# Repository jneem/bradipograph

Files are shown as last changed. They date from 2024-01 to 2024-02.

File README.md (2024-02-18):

# Bradipograph

A drawing robot that's kind of like a [sloth](https://en.wikipedia.org/wiki/Three-toed_sloth),
because it hangs from its arms and moves slowly.

Bradipograph writes its name (https://www.youtube.com/watch?v=CUMBa9waJp0)

This repository contains source code and CAD files for 3d printing. If you want to actually build
one, see the [bradipograph book](https://jneem.github.io/bradipograph).

## Acknowledgements

This project was based on Fredrik Stridsman's
[Stringent](https://www.hackster.io/fredrikstridsman/stringent-the-15-wall-plotter-d965ca)
wall plotter.

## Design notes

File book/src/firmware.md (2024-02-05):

# Firmware and software installation

Bradipograph needs two pieces of software to run: the firmware that gets flashed
onto the bradipograph itself, and the control software that gets run on your
computer.

## Obtain the feeder

Currently, the control software (the "feeder") is only built and tested on x86_64 linux; a statically-linked executable
is available [here](https://github.com/jneem/bradipograph/releases/latest/download/bradipo-feeder). After downloading it
and marking it executable, you should be able to run it:

```
./bradipo-feeder --help

Usage: bradipo-feeder [OPTIONS] [COMMAND]

Commands:
  calibrate        Calibrate the bradipograph from scratch
  set-arm-lengths  Re-calibrate just the arm lengths
  set-max-hang     Set the maximum vertical hang
  set-min-angle    Set the minimum hanging angle
  move             Move to a coordinate
  svg              Draw an SVG file
  square           Draw a square showing the drawable region
  query            Query the current bradipograph status
  help             Print this message or the help of the given subcommand(s)

Options:
      --simulate <SIMULATE>  If set, simulates a bradipograph and draws its output to an svg file at the given path
  -h, --help                 Print help
```

The feeder should also run on Windows and macOS, but you'll need to figure it out yourself;
the source code is [here](https://github.com/jneem/bradipograph/tree/main/crates/feeder).

## Flash the firmware

1. Install `espflash` by following its [installation instructions](https://github.com/esp-rs/espflash/blob/main/espflash/README.md#installation).
2. Download the latest bradipograph [firmware](https://github.com/jneem/bradipograph/releases/latest/download/bradipograph) and the [partition map](https://github.com/jneem/bradipograph/releases/latest/download/partition.csv).
3. Connect your ESP32-C3 (part number 5 in [Materials](./materials.md#other-parts)) to your computer with a USB cable. Your device should
   show up as a serial port; note its name. (On my linux system, it's usually `/dev/ttyACM0`.)
4. Flash your device:
    ```
    espflash flash <path/to/bradipograph> -p </path/to/serial> --partition-table <path/to/partition.csv>
     ```
    where you'll replace `<path/to/bradipograph>` with the location of the bradipograph firmware you downloaded in step 2,
    `<path/to/partition.csv>` with the location of the partition map you downloaded in step 2, and
    `</path/to/serial>` with the serial port that appeared in step 3.
5. With your ESP32-C3 still plugged in, test it by running the feeder. It should find your bradipograph device and see
   that it hasn't been calibrated yet:

   ```
   ./bradipo-feeder query
   calibration: Uncalibrated
   ```

With the firmware set up, you're ready to proceed with [assembly](./assembly.md).

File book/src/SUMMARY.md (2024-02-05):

# Summary

[Bradipograph](./introduction.md)

- [Materials](./materials.md)
- [Firmware](./firmware.md)
- [Assembly](./assembly.md)

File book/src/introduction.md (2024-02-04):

# Bradipograph: the sloth-writer

drawing of a sloth writing on a blackboard

Bradipograph is an open-source build-it-yourself robot for drawing on windows
and blackboards. Controlled over bluetooth, it can draw svgs and comes with a
library of tools for procedurally generating line drawings.

This book contains instructions to build and run your own bradipograph. Assembly
requires a 3d printer, a soldering iron, and about $20 worth of parts.

<iframe width="560" height="315" src="https://www.youtube.com/embed/CUMBa9waJp0?si=j0FrZjRh3RzgkcFA" title="Bradipograph writes its name" frameborder="0" allow="accelerometer; autoplay; clipboard-write; encrypted-media; gyroscope; picture-in-picture; web-share" allowfullscreen></iframe>

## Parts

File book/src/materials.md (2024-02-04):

# List of materials

## 3d printed parts

STL files for 3d printing are available [here](https://github.com/jneem/bradipograph/releases/tag/latest).
The required tolerances are not very tight; any reasonable print settings should be fine.

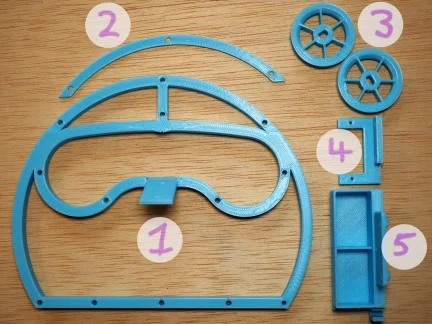
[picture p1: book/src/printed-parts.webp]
picture of 3d printed parts


1. head
2. forehead
3. rotors (you'll need two copies)
4. servo mount
5. battery box

## Other parts

Here is a picture of most of the other parts you'll need (I forgot to include the batteries). I've tried
to include Amazon and AliExpress purchase links where possible, but they tend to go stale. See the [Notes](#notes)
section for more details on the parts, and some advice on substitutions.

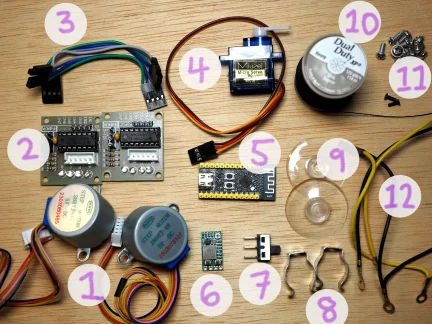
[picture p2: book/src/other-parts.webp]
picture of misc parts


1. two stepper motors (28BYJ-48) ([amazon](https://www.amazon.com/ELEGOO-28BYJ-48-ULN2003-Stepper-Arduino/dp/B01CP18J4A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), [aliexpress](https://www.aliexpress.us/item/2251832520244758.html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))
2. two stepper motor drivers (ULN2003); often sold in combination with the motors
3. the wires that came with my stepper motors and drivers. You can also just supply your own wires.
4. servo motor (sg90) ([amazon](https://www.amazon.com/Hosyond-Helicopter-Airplane-Control-Arduino/dp/B09GFN98X9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), [aliexpress](https://www.aliexpress.us/item/3256806217912283.html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))
5. ESP32-C3FH4 dev board by WeAct Studio ([aliexpress](https://www.aliexpress.us/item/3256804996835770.html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))
6. DC step down converter, 5v output ([amazon](https://www.amazon.com/gp/product/B08JZ5FVLC/ref=ppx_yo_dt_b_search_asin_title?ie=UTF8&psc=1), [aliexpress](https://www.aliexpress.us/item/3256805479283495.html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))
7. Power switch ([amazon](https://www.amazon.com/gp/product/B099N61GTZ/ref=ppx_yo_dt_b_search_asin_title?ie=UTF8&psc=1), [aliexpress](https://www.aliexpress.us/item/2255801021214741.html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))
8. Terry clips, big enough to firmly hold your markers ([amazon](https://www.amazon.com/Terry-Clips-Plastic-Coated-Spring/dp/B09MWGG883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), [aliexpress](https://www.aliexpress.us/item/3256805934884969.html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))
9. Suction cups, ([amazon](https://www.amazon.com/Pawfly-Suction-Without-Decoration-Organization/dp/B08ZS7MV1K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))
10. Thread (or fishing line)
11. A bunch of M3 screws, and two M2 screws.
12. Assorted wires, with "Dupont" style connectors and ring terminals ([amazon](https://www.amazon.com/IWISS-1550PCS-Connector-Headers-Balancer/dp/B08X6C7PZM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), [amazon](https://www.amazon.com/Terrans-Non-Insulated-Terminals-Tin-Plated-Assortment/dp/B0732XSDQX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), [aliexpress](https://www.aliexpress.us/item/3256805929468763.html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), [aliexpress](https://www.aliexpress.us/item/3256806062864141.html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,scm-url:1007.40050.354490.0,pvid:83674697-4719-4718-81c2-e83413735ee2,tpp_buckets:668%232846%238112%231997&pdp_npi=4%40dis%21USD%216.95%210.99%21%21%2149.67%217.04%21%402103010f17070748616161250eef4e%2112000036464995086%21rec%21US%21%21AB&utparam-url=scene%3ApcDetailTopMoreOtherSeller%7Cquery_from%3A))
13. Two 9v rechargeable batteries, and two 9v battery connectors (not pictured)

## Tools and equipment

- soldering iron
- 3d printer
- screwdriver
- hot glue gun
- tool for cutting and stripping wire
- crimping tool
- USB-C data cable
- computer

## Notes

### Motors and servos

28BYJ-48 stepper motors are made by many manufacturers, and often packaged
with ULN2003 drivers.
As of me writing this, a pack of 5 motors and 5 drivers is available
for $15 on Amazon or $10 on AliExpress.

The pen is lifted with an SG90 servo, which is also made by many manufacturers. A 5-pack costs about $10 on Amazon,
or $5 on AliExpress.

### The batteries

I'm using two rechargeable 9v Li-ion batteries. At about $20 for a 4-pack
on Amazon, this is definitely the most expensive part. You'll also need two 9v
battery connectors with wire leads. A 10-pack is about $5 on Amazon.

### Power supply

We'll power the device with 9v batteries, but that 9v needs to be converted
down to 5v. Adjustable DC step-down converters are available in packs
of 5 for about $10 on Amazon or $5 on AliExpress. Any cheap converter should be
fine; we won't draw much current.

### The brains

The device is controlled by an ESP32-C3 chip. Development boards with ESP32-C3
chips are available on AliExpress for as little as $2. There doesn't seem to
be much difference between the different boards except for the locations of the
various pins; probably any of them
will work. But if you want to use the exact same board as me, I'm using
WeAct Studio's ESP32-C3FH4 Core Board. This seems to be available only on AliExpress.

### Pen holder

I'm using two terry clips to hold the marker in place. You can also use a binder clip,
a rubber band, or anything else that holds the pen firmly in place.

### Wiring

I cut my own wires to approximately the correct length; I connected the wires to the
various devices using "Dupont"-style connectors, and I connected the power wires
to one another using a screw and ring terminals. You can of course use pre-cut and
pre-crimped wires if you prefer.

### String

You'll need a few meters of string for hanging the device. Ordinary sewing thread works well
(it isn't very heavy), as does fishing line.

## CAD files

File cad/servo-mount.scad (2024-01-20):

ServoDimensions = [22.5, 12.25];
WallThickness = 5;
ExtraOffset = 3;
Height = 4;
ServoScrewDistance = 27.5;
MountScrewDistance = 17;
MountScrewHeight = 8;

$fn=100;

difference() {
    translate([-ServoDimensions[0] / 2 - WallThickness, - ServoDimensions[1] / 2 - WallThickness - ExtraOffset])
    cube([ServoDimensions[0] + 2 * WallThickness, ServoDimensions[1] + WallThickness + ExtraOffset, Height]);
    cube([ServoDimensions[0] + 0.01, ServoDimensions[1] + 0.01, 20], center = true);
    
    // Screw holes for attaching to the servo
    translate([ServoScrewDistance / 2, 0, 0]) cylinder(20, r=0.95, center = true);
    translate([-ServoScrewDistance / 2, 0, 0]) cylinder(20, r=0.95, center = true);
}

translate([ServoDimensions[0] / 2 + WallThickness - MountScrewDistance / 2 - 3, 0, 0])
difference() {
    h = MountScrewHeight + 3;
    w = MountScrewDistance + 6;
    translate([0, -ServoDimensions[1]/2 - WallThickness - ExtraOffset/2, h/2])
    cube([w, ExtraOffset, h], center = true);
    
    translate([MountScrewDistance / 2, 0, MountScrewHeight])
    rotate([90, 0, 0])
    cylinder(50, r=1.5, center = true);

    translate([- MountScrewDistance/2, 0, MountScrewHeight])
    rotate([90, 0, 0])
    cylinder(50, r=1.5, center = true);
}

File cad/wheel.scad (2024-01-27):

// Diameter of (the round part of) the shaft.
ShaftDiameter = 5.0;

// Width of the flat part of the shaft;
ShaftFlatWidth = 3.0;

// The radius of the wheel, measured at the deepest part of the V
WheelRadius = 13;

// The outer radius of the hub
HubRadius = 5;

// Total thickness of the wheel
Thickness = 6;

// Radius of the rim cut-out for the string
StringRadius = 0.8;

$fs = 0.4;
$fa = 1;

module RimCrossSection() {
    t = Thickness / 2;
    rotate(-90)
    polygon([[0, 0], [t, t], [t, 0], [t/2, -t/2],
             [-t/2, -t/2], [-t, 0], [-t, t]]);
}

module Rim() {
    difference() {
        rotate_extrude()
        translate([WheelRadius, 0, 0]) 
        RimCrossSection();
        
        t = WheelRadius + StringRadius * sqrt(2);
        translate([t, 0, 0]) rotate([0, -45, 0]) cylinder(10, StringRadius, StringRadius, center = true);
        translate([t, 0, 0]) rotate([0, 45, 0]) cylinder(10, StringRadius, StringRadius, center = true);
    }
}

module Shaft() {
    intersection() {
        cylinder(Thickness * 2, ShaftDiameter / 2, ShaftDiameter / 2, center = true);
        cube([ShaftFlatWidth, ShaftDiameter * 2, Thickness * 2], center = true);
    }
}

module Hub() {
    difference() {
        cylinder(Thickness, HubRadius, HubRadius, center = true);
        Shaft();

    }
}

module Spoke2d() {
    // Distance from the end of the spoke to the origin. Should be inside the hub
    // somewhere.
    dist = ShaftDiameter / 2 + (HubRadius - ShaftDiameter / 2) / 2;
    h = WheelRadius + Thickness / 2 - dist;
    difference() {
        translate([h/2 + dist, 0])
        square([h, Thickness], center = true);
        
        translate([WheelRadius + 0.2, 0])
        minkowski() {
            translate([Thickness / 2, 0]) square([Thickness, 0.1], center = true);
            RimCrossSection();
        };
    }
}
module Spoke() {
    rotate([90, 0, 0])
    linear_extrude(1, center = true) Spoke2d();
}

module Wheel() {
for (deg = [0:60:360]) {
    rotate([0, 0, deg+30]) Spoke();
}

Hub();
Rim();
}

Wheel();

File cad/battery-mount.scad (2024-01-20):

BatterySize = [26.2, 16.9];
WallThickness = 1;
BackOffset = 2;
BoxHeight = 15;
ScrewOffset = 2.5;
ChinDepth = 2.5;
PlateWidth = 30;
PlateHeight = 15;
PowerRegulatorWidth = 11;

$fn=100;

module Box() {
    translate([-BatterySize[0] - WallThickness * 1.5, 0, 0])
    cube([BatterySize[0] * 2 + WallThickness * 3, BatterySize[1] + WallThickness * 2 + BackOffset, BoxHeight]);
    
    hull() {
        translate([-BatterySize[0] - WallThickness * 1.5, -ChinDepth, BoxHeight - 0.01])
        cube([BatterySize[0] * 2 + WallThickness * 3, ChinDepth, 0.01]);
        
        translate([-BatterySize[0] - WallThickness * 1.5, 0, BoxHeight - 0.01 - ChinDepth])
        cube([BatterySize[0] * 2 + WallThickness * 3, ChinDepth, 0.01]);
    }
}

module Battery() {
    module Right() {
        translate([WallThickness / 2, WallThickness + BackOffset, WallThickness])
        cube([BatterySize[0], BatterySize[1], 50]);
    }
    
    Right();
    mirror([1,0,0]) Right();

    // Cut the middle piece a little for better access to the screw.
    translate([-BatterySize[0] / 2, WallThickness + BackOffset, WallThickness + BoxHeight - 4])
    cube([BatterySize[0], BatterySize[1], 50]);
}

module ElectricScrewSupport() {
    h = 1.5;
    rotate([90, 0, 0])
    translate([0, 0, h/2]) cylinder(h, r1= 3, r2 = 2, center = true);
}

module Hanger() {
    module Support() {
        translate([0, BackOffset, BoxHeight + ScrewOffset - 2])
        rotate([90, 0, 0])
        linear_extrude(BackOffset)
        offset(r=2) translate([-PlateWidth / 2, 0]) square([PlateWidth, PlateHeight]);
    }

    translate([PlateWidth / 2 - 3, 0, BoxHeight + ScrewOffset + PlateHeight - 3])
    ElectricScrewSupport();
    translate([-PlateWidth / 2 + 3, 0, BoxHeight + ScrewOffset + PlateHeight - 3])
    ElectricScrewSupport();
    
    Support();
}

module ScrewHoles() {
    translate([0, 0, BoxHeight + ScrewOffset])
    rotate([90, 0, 0])
    cylinder(30, r=1.5, center = true);

    translate([PlateWidth / 2 - 3, 0, BoxHeight + ScrewOffset + PlateHeight - 3])
    rotate([90, 0, 0])
    cylinder(30, r=1.45, center = true);

    translate([-PlateWidth / 2 + 3, 0, BoxHeight + ScrewOffset + PlateHeight - 3])
    rotate([90, 0, 0])
    cylinder(30, r=1.45, center = true);
}

module PowerRegulator() {
    h = 5;
    d = 4;
    translate([0, - PowerRegulatorWidth / 2 - WallThickness, h/2])
    difference() {
        cube([d, PowerRegulatorWidth + WallThickness * 2, 5], center = true);
        translate([0, 0, WallThickness])
        cube([d + 0.01, PowerRegulatorWidth, 5.01], center = true);
    }
}

module PowerSwitch() {
    h = 10;
    d = 6;

    translate([-3.5, 0, h / 2])
    difference() {
        cube([7, d, h], center = true);
        translate([0, 0, 2]) cube([3, d + 0.01, h], center = true);
    }
}


module Positive() {
    Box();
    Hanger();

    translate([-BatterySize[0] - WallThickness * 1.5, BatterySize[1] + WallThickness * 2 + BackOffset, 0])
    PowerRegulator();

    translate([-BatterySize[0] - WallThickness * 1.5, 0, 0])
    PowerSwitch();
}

module Negative() {
    Battery();
    ScrewHoles();
}

difference() {
    Positive();
    Negative();
}

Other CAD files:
cad/main.scad

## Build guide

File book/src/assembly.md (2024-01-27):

# Assembly instructions

## Mount the motor drivers

Turn the head face-down, and place a stepper driver face-down in
the bottom left-hand corner, with the four LEDs on the driver towards
the top of the head. Secure with two M3 screws, then repeat with the other
stepper driver in the bottom right-hand corner of the head.

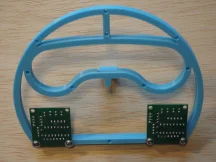
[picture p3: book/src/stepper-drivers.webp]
head with stepper drivers attached


## Attach the motors

With the head still face-down, turn one of the stepper motors axle-down
and mount it with two M3 screws to the left eye socket. The motor's wires
should point towards the bottom of the head, and slightly to the left.
Mount the other stepper motor to the right eye socket.

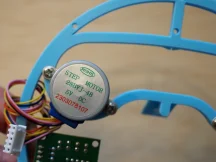
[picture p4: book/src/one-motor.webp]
head with one motor attached

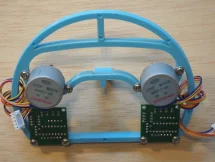
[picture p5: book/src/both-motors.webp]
head with both motors attached


## Attach the strings

Cut two long pieces of thread. Find the two holes in the rim of one
of the rotors. Starting from outside the rotor, insert the end of the
thread into one hole, then pass it between the spokes, then bring
it back out through the other hole.

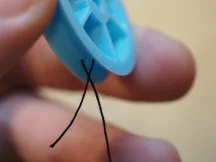
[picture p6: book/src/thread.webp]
rotor with a thread passing through the rim holes

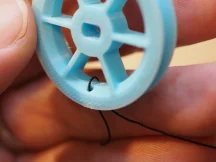
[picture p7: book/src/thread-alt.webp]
rotor with a thread passing through the rim holes, alternate angle


Tie a knot in the thread and cut off the excess.

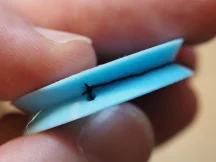
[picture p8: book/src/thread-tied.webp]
rotor with a thread tied through the rim holes


Tie the other end of the thread to one of the suction cups, and wind the thread around
the rotor.

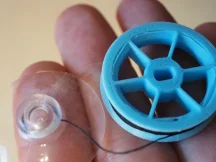
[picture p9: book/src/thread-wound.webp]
rotor with a thread wound around it


Repeat with the other rotor, thread, and suction cup.

## Mount the rotors

Turn the head face-up, and orient one rotor so that the thread winds
counter-clockwise around it. Press the rotor onto the axle of the left motor.
It should be a snug fit, and may require some force.
Pass the thread through the thread guide.

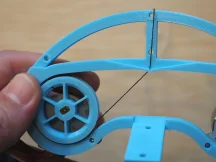
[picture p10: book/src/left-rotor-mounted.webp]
left rotor attached to the head


Mount the right rotor, oriented so that its thread winds clockwise. When
passing its thread through the thread guide, cross it over the left
rotor's thread.

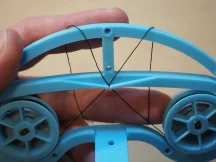
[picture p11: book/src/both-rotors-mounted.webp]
both rotors attached to the head


Wind the motor wires around the sides of the head to use up the excess,
then plug them into the motor drivers.

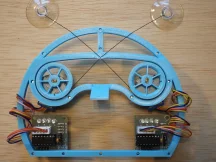
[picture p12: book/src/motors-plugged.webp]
the motor wires plugged in


Making sure that the threads are crossed, place the forehead piece over
the threads and attach it with two M3 screws. Don't attach the middle screw yet!

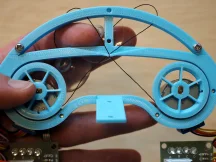
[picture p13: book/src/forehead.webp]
forehead screwed to the head


## Mount the servo

Turn the head face-down, and mount the servo bracket to the back of the head with
two M3 screws.
The servo attachment points should be on the right, and extend above the top
of the head as shown.

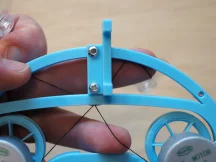
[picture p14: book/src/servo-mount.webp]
servo mounted to the head


The top screw of the servo mount must be at least 12mm, so it is long enough to
extend through the forehead.

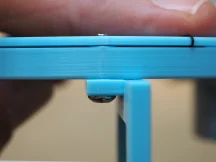
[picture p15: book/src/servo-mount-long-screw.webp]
upper servo-mount screw extending through the forehead


Insert the servo into its bracket from the right, with the servo axle towards the bottom of the head.
Fasten the servo to its bracket with two M2 screws, passing them through the servo's screw holes first
and then into the bracket.

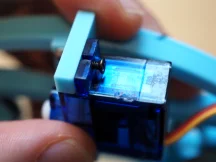
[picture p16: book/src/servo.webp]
servo mounted to the bracket

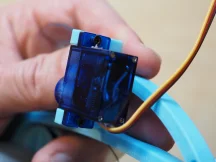
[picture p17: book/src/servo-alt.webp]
servo mounted to the bracket, alternate angle


## Attach the battery box

Attach the 9v battery connectors to the voltage converter and the power switch:
1. Solder the two positive wires from the battery connectors to center pin of the switch.
2. Join the two negative wires from the battery connector, and crimp on a ring terminal.
3. Solder a wire from one of the other switch pins to the "IN+" pin of the voltage converter.
4. Solder wires to the "GND" and "VO+" pins of the voltage converter, and crimp ring terminals
   to the other ends.

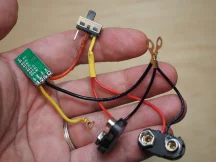
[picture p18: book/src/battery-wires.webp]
battery connectors, wired up to voltage converter and power switch


Using a hot glue gun, glue the voltage converter and the power switch to their mounting points
at the bottom left of the battery box.

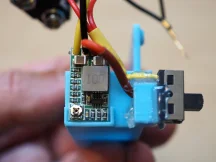
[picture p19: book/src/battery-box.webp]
voltage converter and power switch glued to the battery box

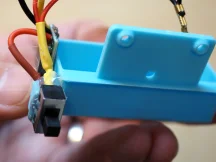
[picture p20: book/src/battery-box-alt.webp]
voltage converter and power switch glued to the battery box, alternate angle


Turn the head face-down, and use an M3 screw to attach the battery box to the bottom part of
the head, between the two stepper drivers.

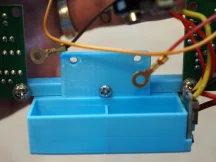
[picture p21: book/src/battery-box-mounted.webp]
battery box mounted to the head


## Attach the pen holder

Using M3 screw, attach the two spring clips to the nose.

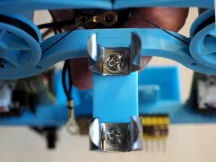
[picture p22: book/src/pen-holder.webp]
pen holder mounted to the nose


## Wire up the stepper drivers

Connect the stepper drivers to the dev board, paying close attention to the orientation.
Each stepper driver has four pins in its bottom left-hand corner; pin 1 is on the left and pin 4 is on the right.
Connect pins 1, 2, 3, and 4 of the left stepper driver to pins 0, 1, 2, and 3 respectively on the
dev board. Connect pins 1, 2, 3, and 4 of the right stepper driver to pins 4, 5, 6, and 7 respectively
on the dev board.

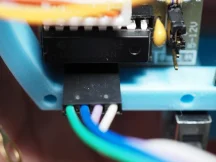
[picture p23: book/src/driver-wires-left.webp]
driver wires connected to the left driver

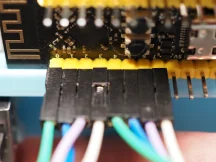
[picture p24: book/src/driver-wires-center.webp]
driver wires connected to the dev board

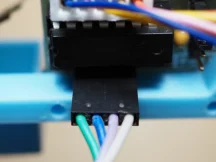
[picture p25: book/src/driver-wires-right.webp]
driver wires connected to the right driver


Cut and strip the ends of the servo motor wires. Crimp ring terminals to the ends of the red and brown
wires, and crimp a DuPont connector to the end of the yellow wire. Plug the yellow wire into pin 10 of
the dev board.

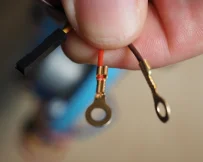
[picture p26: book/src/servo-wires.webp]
servo wire ends

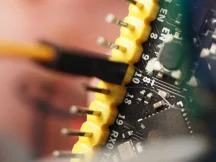
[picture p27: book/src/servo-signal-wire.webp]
servo signal wire connected to the dev board


Prepare two 2x1 DuPont connectors for providing power to the stepper drivers: first, crimp a power wire and
a ground wire to each connector. Join the two power wires and crimp them to a ring terminal, then join the
two ground wires and crimp them to another ring terminal.

## Wire up the power

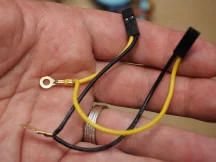
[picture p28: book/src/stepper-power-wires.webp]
stepper power wires


Plug the stepper power connectors into the stepper drivers.

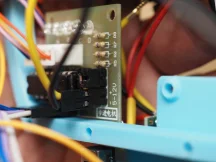
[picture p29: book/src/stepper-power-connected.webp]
stepper power wires, plugged into the drivers


Prepare a 3x1 DuPont connector for providing power to the dev board. Leaving the middle pin empty, crimp
a power wire and a ground wire into the two outer pins.

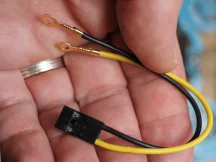
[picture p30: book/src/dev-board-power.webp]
dev board power wires


Plug in the dev board power so that the power wire connects to the pin labeled "5V" and the ground wire
connects to one of the pins labeled "G".

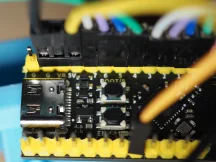
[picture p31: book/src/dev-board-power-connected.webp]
dev board power wires, plugged into the dev board


Gather all the 5V power wires (the red wire from the servo, the wire from the "VO+" pin of the voltage converter,
the stepper driver power wires, and the dev board power wire). Put an M3 screw through the ring terminals of all
these wires and screw it into the left hole on the battery box.

Gather all the ground wires (the brown wire from the servo, the wire from the "GND" pin of the voltage converter,
the stepper driver ground wires, the dev board ground wire, and the wire from the negative 9V battery terminal).
Put an M3 screw through the ring terminals of all
these wires and screw it into the right hole on the battery box.

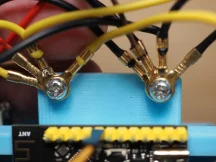
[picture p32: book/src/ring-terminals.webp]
ring terminals, all screwed together


Plug 9v batteries into the battery connectors, and put them in the battery box.

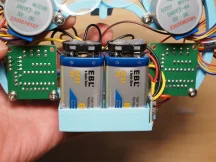
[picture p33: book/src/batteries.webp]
batteries plugged in


## Align the servo motor

Turn on the power switch. The first two leds on each stepper motor should light up, and you should here
a sound as the servo moves into position. Turn the power switch off again.

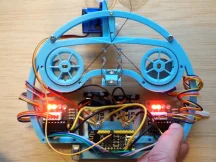
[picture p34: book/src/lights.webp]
lights on


Now that the servo has found its position, attach the little plastic piece to the servo axle so that it
points perpendicularly out from the back of the head.

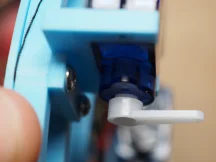
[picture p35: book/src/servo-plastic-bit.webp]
servo motor plastic bit sticking out


And that's it! Your Bradipograph is assembled and ready to draw.

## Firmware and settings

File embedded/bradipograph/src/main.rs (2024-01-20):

#![no_std]
#![no_main]
#![feature(type_alias_impl_trait)]

use core::cell::Cell;

use bradipo_geom::{Config, ConfigBuilder, LenExt as _, StepperPositions};
use bradipo_protocol::{Calibration, Cmd, StepperSegment};
use embassy_executor::Spawner;
use embassy_sync::blocking_mutex::raw::CriticalSectionRawMutex;
use embassy_time::Timer;
use embedded_storage::{ReadStorage, Storage};
use esp32c3_hal::{
    clock::{ClockControl, Clocks},
    embassy,
    ledc::{self, timer, LSGlobalClkSource, LowSpeed, LEDC},
    peripherals::Peripherals,
    prelude::*,
    systimer::{self},
    timer::TimerGroup,
    Rng, IO,
};
use esp_backtrace as _;
use esp_println::println;
use esp_storage::FlashStorage;
use esp_wifi::EspWifiInitFor;
use heapless::spsc::Queue;
use servo::Servo;
use stepper::{Direction, Stepper};

mod ble;
mod servo;
mod stepper;

macro_rules! singleton {
    ($val:expr, $T:ty) => {{
        static STATIC_CELL: ::static_cell::StaticCell<$T> = ::static_cell::StaticCell::new();
        STATIC_CELL.init($val)
    }};
}

use ble::{ble_task, CmdConsumer};

pub type Channel<T, const N: usize> = embassy_sync::channel::Channel<CriticalSectionRawMutex, T, N>;
pub type Sender<T, const N: usize> =
    embassy_sync::channel::Sender<'static, CriticalSectionRawMutex, T, N>;
pub type Receiver<T, const N: usize> =
    embassy_sync::channel::Receiver<'static, CriticalSectionRawMutex, T, N>;
pub type Mutex<T> = embassy_sync::blocking_mutex::Mutex<CriticalSectionRawMutex, T>;

const FLASH_ADDR: u32 = 0x110000;

static GLOBAL: GlobalState = GlobalState {
    config: Mutex::new(Cell::new(None)),
    position: Mutex::new(Cell::new(None)),
    pen_down: Mutex::new(Cell::new(false)),
};

struct GlobalState {
    config: Mutex<Cell<Option<Config>>>,
    position: Mutex<Cell<Option<StepperPositions>>>,
    pen_down: Mutex<Cell<bool>>,
}

impl GlobalState {
    pub fn config(&self) -> Option<Config> {
        self.config.lock(|c| c.get())
    }

    pub fn position(&self) -> Option<StepperPositions> {
        self.position.lock(|p| p.get())
    }

    pub fn pen_down(&self) -> bool {
        self.pen_down.lock(|p| p.get())
    }

    pub fn set_config(&self, config: Config) {
        self.config.lock(|c| c.set(Some(config)));
    }

    pub fn modify_config(&self, f: impl FnOnce(&mut Config)) {
        self.config.lock(|cell| {
            if let Some(mut c) = cell.get() {
                f(&mut c);
                cell.set(Some(c));
            }
        });
    }

    pub fn set_position(&self, pos: StepperPositions) {
        self.position.lock(|p| p.set(Some(pos)));
    }

    pub fn set_pen_down(&self, down: bool) {
        self.pen_down.lock(|p| p.set(down));
    }

    pub fn write_to_flash(&self) {
        if let (Some(config), Some(position)) = (self.config(), self.position()) {
            let mut buf = [0u8; 256];
            buf[0..5].copy_from_slice(b"bradi");
            let mut flash = FlashStorage::new();
            let data = FlashData { config, position };
            let _ = postcard::to_slice(&data, &mut buf[5..]).unwrap();
            flash.write(FLASH_ADDR, &buf).unwrap();
        }
    }

    pub fn read_from_flash(&self) -> Option<(Config, StepperPositions)> {
        let mut buf = [0u8; 256];
        let mut flash = FlashStorage::new();
        flash.read(FLASH_ADDR, &mut buf).unwrap();

        if &buf[0..5] == b"bradi" {
            let data = postcard::from_bytes::<FlashData>(&buf[5..]).ok()?;
            self.set_config(data.config);
            self.set_position(data.position);
            Some((data.config, data.position))
        } else {
            None
        }
    }
}

fn apply_calibration(global: &GlobalState, calib: Calibration) -> (Config, StepperPositions) {
    let radius = 1.35.cm();

    let config = if let Some(mut prev_config) = global.config() {
        prev_config.claw_distance = calib.claw_distance;
        // TODO: make these configurable, and don't override them here
        prev_config.spool_radius = radius;
        prev_config.steps_per_revolution = 2036.0;
        prev_config
    } else {
        ConfigBuilder::default()
            .with_claw_distance(calib.claw_distance)
            .with_spool_radius(radius)
            .with_max_hang(30.0.cm())
            .build()
    };

    let angles = config.arm_lengths_to_rotor_angles(&calib.arm_lengths);
    let pos = config.rotor_angles_to_stepper_steps(&angles);

    global.set_config(config);
    global.set_position(pos);
    global.write_to_flash();
    (config, pos)
}

async fn move_seg(seg: StepperSegment, left: &mut Stepper, right: &mut Stepper) {
    // This is for "underarm" orientation.
    let right_dir = if seg.right_steps > 0 {
        Direction::CounterClockwise
    } else {
        Direction::Clockwise
    };
    let left_dir = if seg.left_steps > 0 {
        Direction::Clockwise
    } else {
        Direction::CounterClockwise
    };

    for tick in seg.iter_steps() {
        Timer::after_micros(tick.delay_us.into()).await;
        if tick.left {
            left.step(left_dir);
        }
        if tick.right {
            right.step(right_dir);
        }
    }
}

async fn calibrated_control(
    mut cmds: CmdConsumer,
    left: &mut Stepper,
    right: &mut Stepper,
    servo: &mut Servo,
) {
    let mut maybe_steps = GLOBAL.position();
    loop {
        let mut written = false;
        let cmd = loop {
            if let Some(cmd) = cmds.dequeue() {
                break cmd;
            }
            if !written {
                // If we get here, our command queue is empty so let's take the
                // opportunity to write our current state to flash.
                GLOBAL.write_to_flash();
                written = true;
            }
            Timer::after_millis(2).await
        };
        match cmd {
            Cmd::Segment(seg) => {
                let Some(mut steps) = maybe_steps else {
                    println!("cannot move without a position");
                    continue;
                };

                steps.left = steps.left.checked_add_signed(seg.left_steps).unwrap();
                steps.right = steps.right.checked_add_signed(seg.right_steps).unwrap();
                maybe_steps = Some(steps);

                move_seg(seg, left, right).await;

                GLOBAL.set_position(steps);
            }
            Cmd::Calibrate(calibration) => {
                let (_, pos) = apply_calibration(&GLOBAL, calibration);

                maybe_steps = Some(pos);
            }
            Cmd::SetMinAngle(deg) => {
                GLOBAL.modify_config(|c| c.min_angle = deg);
                GLOBAL.write_to_flash();
            }
            Cmd::SetMaxHang(h) => {
                GLOBAL.modify_config(|c| c.max_hang = h);
                GLOBAL.write_to_flash();
            }
            Cmd::PenUp => {
                servo.set_angle(90).await;
                GLOBAL.set_pen_down(false);
                GLOBAL.write_to_flash();
                Timer::after_millis(500).await;
            }
            Cmd::PenDown => {
                servo.set_angle(0).await;
                GLOBAL.set_pen_down(true);
                GLOBAL.write_to_flash();
                Timer::after_millis(500).await;
            }
        }
    }
}

#[main]
async fn main(spawner: Spawner) {
    let peripherals = Peripherals::take();
    let system = peripherals.SYSTEM.split();
    let clocks = singleton!(ClockControl::max(system.clock_control).freeze(), Clocks<'_>);
    embassy::init(clocks, TimerGroup::new(peripherals.TIMG0, clocks).timer0);

    let init = esp_wifi::initialize(
        EspWifiInitFor::Ble,
        systimer::SystemTimer::new(peripherals.SYSTIMER).alarm0,
        Rng::new(peripherals.RNG),
        system.radio_clock_control,
        clocks,
    )
    .unwrap();

    let cmd_queue = singleton!(Queue::new(), Queue<Cmd, 64>);
    let (cmd_tx, cmd_rx) = cmd_queue.split();
    spawner.must_spawn(ble_task(init, peripherals.BT, cmd_tx));

    let io = IO::new(peripherals.GPIO, peripherals.IO_MUX);

    let mut right = Stepper::new(
        io.pins.gpio0.into_push_pull_output(),
        io.pins.gpio1.into_push_pull_output(),
        io.pins.gpio2.into_push_pull_output(),
        io.pins.gpio3.into_push_pull_output(),
    );
    let mut left = Stepper::new(
        io.pins.gpio4.into_push_pull_output(),
        io.pins.gpio5.into_push_pull_output(),
        io.pins.gpio6.into_push_pull_output(),
        io.pins.gpio7.into_push_pull_output(),
    );

    let ledc = singleton!(LEDC::new(peripherals.LEDC, clocks), LEDC<'static>);
    ledc.set_global_slow_clock(LSGlobalClkSource::APBClk);
    let lstimer0 = singleton!(
        ledc.get_timer::<LowSpeed>(timer::Number::Timer2),
        ledc::timer::Timer<LowSpeed>
    );
    lstimer0
        .configure(timer::config::Config {
            duty: timer::config::Duty::Duty14Bit,
            clock_source: timer::LSClockSource::APBClk,
            frequency: 50u32.Hz(),
        })
        .unwrap();
    let mut servo_channel = ledc.get_channel::<LowSpeed, _>(
        ledc::channel::Number::Channel0,
        io.pins.gpio10.into_push_pull_output(),
    );
    servo_channel
        .configure(ledc::channel::config::Config {
            timer: lstimer0,
            duty_pct: 3,
            pin_config: ledc::channel::config::PinConfig::PushPull,
        })
        .unwrap();
    let mut servo = Servo::new(servo_channel);
    servo.set_angle(90).await;

    let mut buf = [0u8; 256];
    let mut flash = FlashStorage::new();
    flash.read(FLASH_ADDR, &mut buf).unwrap();

    GLOBAL.read_from_flash();
    calibrated_control(cmd_rx, &mut left, &mut right, &mut servo).await;
}

#[derive(serde::Serialize, serde::Deserialize, Debug)]
struct FlashData {
    config: Config,
    position: StepperPositions,
}

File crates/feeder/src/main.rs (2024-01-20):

#![allow(clippy::redundant_closure_call)]

use std::{
    path::{Path, PathBuf},
    time::Duration,
};

use anyhow::anyhow;
use bradipo_geom::{Angle, ArmLengths, LenExt as _, Point};
use bradipo_protocol::{Calibration, CalibrationStatus, Cmd};
use btleplug::{
    api::{Central as _, Manager as _, ScanFilter},
    platform::Manager,
};
use clap::{builder::ValueParser, CommandFactory, FromArgMatches, Parser, Subcommand};
use connection::{BradipographLike, MockBradipograph};
use indicatif::ProgressBar;
use kurbo::{BezPath, Rect, Shape as _};
use reedline::{DefaultPrompt, DefaultPromptSegment, Prompt, Reedline};

use crate::{connection::Bradipograph, simulator::Simulation};

mod connection;
mod simulator;
mod svg;

const TICK: Duration = Duration::from_millis(50);
const MAX_STEPS_PER_SEC: u32 = 450;
// what fraction of a second does it take to reach max velocity
const MAX_VELOCITY_PER_SEC: f64 = 1.5;

#[derive(Parser)]
struct Args {
    /// If set, simulates a bradipograph and draws its output to an
    /// svg file at the given path.
    #[arg(long)]
    simulate: Option<PathBuf>,

    #[command(subcommand)]
    command: Option<Command>,
}

#[derive(Subcommand)]
enum Command {
    /// Calibrate the bradipograph from scratch
    Calibrate {
        /// distance (in cm) between the two claws
        #[arg(value_parser = ValueParser::new(sane_f32))]
        claw_distance: f32,
        /// length (in cm) of the left arm
        #[arg(value_parser = ValueParser::new(sane_f32))]
        left: f32,
        /// length (in cm) of the right arm
        #[arg(value_parser = ValueParser::new(sane_f32))]
        right: f32,
    },

    /// Re-calibrate just the arm lengths
    SetArmLengths {
        /// length (in cm) of the left arm
        #[arg(value_parser = ValueParser::new(sane_f32))]
        left: f32,
        /// length (in cm) of the right arm
        #[arg(value_parser = ValueParser::new(sane_f32))]
        right: f32,
    },

    /// Set the maximum vertical hang
    SetMaxHang {
        /// maximum distance (in cm) that we can hang below the claws
        #[arg(value_parser = ValueParser::new(sane_f32))]
        hang: f32,
    },

    /// Set the minimum hanging angle
    SetMinAngle {
        /// minimum angle (in degrees)
        #[arg(value_parser = ValueParser::new(sane_f32))]
        angle: f32,
    },

    /// Move to a coordinate
    Move {
        /// `x` coordinate (in cm), with zero being exactly between the two claws
        #[arg(value_parser = ValueParser::new(sane_signed_f32))]
        x: f32,
        /// `y` coordinate (in cm), with zero being the highest drawable position,
        /// and positive values being lower.
        #[arg(value_parser = ValueParser::new(sane_f32))]
        y: f32,
    },

    /// Draw an SVG file
    Svg {
        /// path to the svg input
        path: PathBuf,

        /// scale the output to this width (in cm)
        #[arg(value_parser = ValueParser::new(sane_f32))]
        width: Option<f32>,

        /// scale the output to this width (in cm)
        #[arg(value_parser = ValueParser::new(sane_f32))]
        height: Option<f32>,

        #[arg(long)]
        fill: bool,
    },

    /// Draw a square showing the drawable region
    Square,

    /// Query the current bradipograph status
    Query,
}

async fn reload_simulation(brad: &mut impl BradipographLike) -> Result<Simulation> {
    match brad.read_state().await? {
        CalibrationStatus::Uncalibrated => Err(anyhow!("Calibration mysteriously failed").into()),
        CalibrationStatus::Calibrated(state) => Ok(make_simulation(&state)),
    }
}

async fn calibrate(brad: &mut impl BradipographLike, calib: Calibration) -> Result<Simulation> {
    brad.send_cmd_and_wait(Cmd::Calibrate(calib)).await?;
    reload_simulation(brad).await
}

impl Command {
    async fn execute(
        &self,
        brad: &mut impl BradipographLike,
        simulation: &mut Option<Simulation>,
    ) -> Result<()> {
        match self {
            Command::Calibrate {
                claw_distance,
                left,
                right,
            } => {
                let calib = Calibration {
                    claw_distance: claw_distance.cm(),
                    arm_lengths: ArmLengths {
                        left: left.cm(),
                        right: right.cm(),
                    },
                };
                *simulation = Some(calibrate(brad, calib).await?);
            }
            Command::SetArmLengths { left, right } => match brad.read_state().await? {
                CalibrationStatus::Uncalibrated => {
                    return Err(anyhow!("set-arm-lengths requires calibration").into())
                }
                CalibrationStatus::Calibrated(state) => {
                    let calib = Calibration {
                        claw_distance: state.geom.claw_distance,
                        arm_lengths: ArmLengths {
                            left: left.cm(),
                            right: right.cm(),
                        },
                    };
                    *simulation = Some(calibrate(brad, calib).await?);
                }
            },
            Command::SetMaxHang { hang } => {
                brad.send_cmd_and_wait(Cmd::SetMaxHang(hang.cm())).await?;
                *simulation = Some(reload_simulation(brad).await?);
            }
            Command::SetMinAngle { angle } => {
                brad.send_cmd_and_wait(Cmd::SetMinAngle(Angle::degrees(*angle)))
                    .await?;
                *simulation = Some(reload_simulation(brad).await?);
            }
            Command::Move { x, y } => {
                let Some(sim) = simulation.as_mut() else {
                    return Err(anyhow!("move requires calibration").into());
                };
                let pos = Point::new(*x, *y);
                for cmd in sim.move_to(pos) {
                    brad.send_cmd(cmd).await?;
                }
            }
            Command::Svg {
                path,
                width,
                height,
                fill,
            } => {
                let Some(sim) = simulation.as_mut() else {
                    return Err(anyhow!("svg requires calibration").into());
                };
                let mut rect = sim.geom.draw_box();
                if let Some(width) = width.map(f64::from) {
                    if width < rect.width() {
                        rect.x0 = -width / 2.0;
                        rect.x1 = width / 2.0;
                    }
                }
                if let Some(height) = height.map(f64::from) {
                    if height < rect.height() {
                        let center = rect.center().y;
                        rect.y0 = center - height / 2.0;
                        rect.y1 = center + height / 2.0;
                    }
                }
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

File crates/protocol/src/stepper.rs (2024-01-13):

use serde::{Deserialize, Serialize};

/// The position of the stepper motors, measured in number of steps.
///
/// A zero value corresponds to an arm length of zero, and increasing
/// values correspond to longer arms.
#[derive(Debug, Clone, Copy, PartialEq, Eq, serde::Serialize, serde::Deserialize)]
pub struct StepperPositions {
    pub left: u32,
    pub right: u32,
}

#[derive(Clone, Debug, Serialize, Deserialize)]
pub struct StepperSegment {
    pub left_steps: i32,
    pub right_steps: i32,
    pub start_steps_per_sec: u16,
    pub end_steps_per_sec: u16,
    pub steps_per_sec_per_sec: u32,
}

impl StepperSegment {
    /// If a segment is long and the initial and final velocities are both small, the step
    /// iterator will just move along it very slowly. This is probably not what we want,
    /// though: we want to accelerate to a higher maximum speed, and then decelerate at
    /// the end.
    ///
    /// This method splits a single segment into two: an acceleration segment and a deceleration
    /// segment.
    #[cfg(feature = "std")]
    pub fn split(&self, max_steps_per_sec: u16) -> Option<(StepperSegment, StepperSegment)> {
        let start_v = self.start_steps_per_sec as f64;
        let end_v = self.end_steps_per_sec as f64;
        let max_v = max_steps_per_sec as f64;
        let max_steps_per_sec_per_sec = self.steps_per_sec_per_sec as f64;

        let square = |x| x * x;
        // How many steps would it take to get from the initial to the final velocity?
        let steps = (square(start_v) - square(end_v)).abs() / (2.0 * max_steps_per_sec_per_sec);

        let max_steps = self.left_steps.abs().max(self.right_steps.abs()) as f64;
        if max_steps == 0.0 {
            // Avoid dividing by zero.
            return None;
        }
        if steps <= max_steps / 2.0 && end_v <= max_v * 0.75 {
            // 2 * max_steps * self.accel.steps_per_s_per_s is the total amount that the squared
            // velocity can change while traversing this segment. Some of that change must be used
            // up in getting from the initial velocity to the final velocity. And then the peak energy
            // as we traverse the segment is half of what's left (since we need to go up and then down).
            let max_energy = max_steps * max_steps_per_sec_per_sec
                - (square(start_v) - square(end_v)).abs() / 2.0;
            let max_velocity = max_energy.sqrt().min(max_v);

            // How may steps will it take to get from the max velocity back down to the final velocity?
            let decel_steps =
                (square(max_velocity) - square(end_v)) / (2.0 * max_steps_per_sec_per_sec);

            let decel_seg = StepperSegment {
                left_steps: (self.left_steps as f64 * decel_steps / max_steps).round() as i32,
                right_steps: (self.right_steps as f64 * decel_steps / max_steps).round() as i32,
                start_steps_per_sec: max_velocity as u16,
                end_steps_per_sec: self.end_steps_per_sec,
                steps_per_sec_per_sec: self.steps_per_sec_per_sec,
            };
            let accel_seg = StepperSegment {
                left_steps: self.left_steps - decel_seg.left_steps,
                right_steps: self.right_steps - decel_seg.right_steps,
                start_steps_per_sec: self.start_steps_per_sec,
                end_steps_per_sec: decel_seg.start_steps_per_sec,
                steps_per_sec_per_sec: self.steps_per_sec_per_sec,
            };
            Some((accel_seg, decel_seg))
        } else {
            None
        }
    }

    pub fn iter_steps(&self) -> StepIter {
        let left = self.left_steps.unsigned_abs();
        let right = self.right_steps.unsigned_abs();

        // If either left or right doesn't move, the reciprocal is 1/0. By replacing it by MAX_PARAM,
        // we ensure that the this stepper never wins the "minimum" test that would mark it as the
        // next stepper to move.
        let recip_left_steps = MAX_PARAM.checked_div(left).unwrap_or(MAX_PARAM);
        let recip_right_steps = MAX_PARAM.checked_div(right).unwrap_or(MAX_PARAM);

        // There should be a minimum number of steps. If we say 16, it means that this can
        // be at most 2^19.
        let param_per_steps = MAX_PARAM.saturating_div(left.max(right));

        // We impose a minimum velocity so that we don't wait forever until the first step.
        // A sensible value would be sqrt(accel / 2), since that's the velocity after a
        // single step. We mostly rely on the caller to set the minimum velocity, though.
        //
        // The effect of the saturating_mul here is that the velocity will get truncated
        // if (1) it's fast and (2) there are very few steps. This truncation is probably
        // fine, because it will be over soon anyway.
        let start_param_per_t = (self.start_steps_per_sec as u32)
            .max(16)
            .saturating_mul(param_per_steps);

        let end_param_per_t = (self.end_steps_per_sec as u32)
            .max(16)
            .saturating_mul(param_per_steps);

        let param_per_t_per_t = self.steps_per_sec_per_sec.saturating_mul(param_per_steps);

        StepIter {
            left: 0,
            right: 0,
            max_left: left,
            max_right: right,
            param: 0,
            recip_left_steps,
            recip_right_steps,
            param_per_t: start_param_per_t,
            param_per_t_min: start_param_per_t.min(end_param_per_t),
            param_per_t_max: start_param_per_t.max(end_param_per_t),
            param_per_t_per_t,
            debounce: recip_right_steps.min(recip_left_steps) / 16,
            speeding_up: end_param_per_t > start_param_per_t,
        }
    }
}

#[derive(Clone, Copy, Debug)]
pub struct Tick {
    pub left: bool,
    pub right: bool,
    pub delay_us: u32,
}

const MAX_PARAM: u32 = 1 << 24;

#[derive(Debug)]
pub struct StepIter {
    // These can't actually go all the way up to u32::MAX. Up to 2^24 is probably ok, but I haven't checked carefully.
    max_left: u32,
    max_right: u32,

    // Current position.
    left: u32,
    right: u32,

    // Current parametrization, as a fraction of the distance from
    // the start position to the end position. This maxes out at 2^24.
    param: u32,

    // Current speed, in param per unit time. This goes up to 2^32 - 1, meaning
    // that the fastest we can get through the whole parameter space is about 1/256
    // of a second.
    param_per_t: u32,

    // Measured in the same units as `param`, if two steps happen closer than this
    // we make them happen at the same time.
    debounce: u32,

    // These are relative to MAX_PARAM, in that (modulo rounding errors) recip_left_steps * left_steps = MAX_PARAM.
    recip_left_steps: u32,
    recip_right_steps: u32,

    param_per_t_min: u32,
    param_per_t_max: u32,
    param_per_t_per_t: u32,

    speeding_up: bool,
}
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

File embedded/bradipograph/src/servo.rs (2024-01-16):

use embassy_time::Timer;
use esp32c3_hal::{
    gpio::{GpioPin, Output, PushPull},
    ledc::{
        channel::{Channel, ChannelHW as _},
        LowSpeed,
    },
};

pub struct Servo {
    channel: Channel<'static, LowSpeed, GpioPin<Output<PushPull>, 10>>,
    current_duty: u16,
}

impl Servo {
    pub fn new(ch: Channel<'static, LowSpeed, GpioPin<Output<PushPull>, 10>>) -> Self {
        Self {
            channel: ch,
            current_duty: Servo::duty_for_angle(90),
        }
    }

    pub fn duty_for_angle(deg: u8) -> u16 {
        let duty_exp = 14;
        let duty_range: u32 = 1 << duty_exp;
        (4 * duty_range / 100 + deg as u32 * 8 * duty_range / (100 * 180)) as u16
    }

    pub async fn set_angle(&mut self, deg: u8) {
        // 0 degrees is 4% duty; 180 degrees is 12% duty.
        let duty = Self::duty_for_angle(deg);

        // One pwm cycle is 20ms. Do the movement over 16 cycles (320ms).
        let diff = duty.abs_diff(self.current_duty);
        if diff < 32 {
            self.channel.set_duty_hw(duty as u32);
        } else {
            self.channel.start_duty_fade_hw(
                self.current_duty as u32,
                duty > self.current_duty,
                32,
                1,
                diff / 32,
            );
            Timer::after_millis(320).await;
            while self.channel.is_duty_fade_running_hw() {
                Timer::after_millis(1).await;
            }

            // This should be basically the duty already, but compensate for any rounding errors.
            self.channel.set_duty_hw(duty as u32);
        };
        self.current_duty = duty;
    }
}

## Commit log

2023-12-07 Checkpoint on calibration
2023-12-10 Calibration in the feeder
2023-12-11 Shrink calibration reads, to not overflow the tiny MTU
2023-12-11 Don't race with the calibration command
2023-12-12 Make the calibration persistent
    [partition.csv]
2023-12-13 Rewrite the stepper planner to use (integer) division
2023-12-15 Bump dep versions, and change calibration to use measurements
2023-12-16 Fix stepper scheduling issues, hopefully
    [main.rs, stepper.rs]
2023-12-21 Move the geometry to the host. It was too slow
    [connection.rs, lib.rs, main.rs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]
2023-12-21 Less float computations on the device
2023-12-22 Move the steppers out of planner
2023-12-22 Remove the steppers from planner completely
2023-12-22 Fix steps -> point calculation
    [lib.rs, main.rs]
2023-12-22 Fix position conversion in main
    [main.rs]
2023-12-22 Fix lots of planning bugs
    [lib.rs, main.rs]
2023-12-24 Make capacity queryable, and make servo smoother
2023-12-27 Switch to the weact board
2023-12-30 Add cad files
    [battery-mount.scad, main.scad, servo-mount.scad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]
2024-01-02 Fix continuity detection and svg transform
    [main.rs]
2024-01-05 WIP on another frame revision
    [main.scad]
2024-01-06 Make the device fill
2024-01-06 Next frame revision
    [main.scad]
2024-01-08 Tweak string holder a little
    [main.scad]
2024-01-14 Put power terminals on the battery mount
    [battery-mount.scad]
2024-01-20 Move stepper drivers down, tweak power switch holder
    [battery-mount.scad, main.scad, servo-mount.scad]
2024-01-20 Add assembly outline to book
2024-01-27 Assembly instructions
    [washer.scad, wheel.scad]
2024-02-04 Add introduction, and update materials
